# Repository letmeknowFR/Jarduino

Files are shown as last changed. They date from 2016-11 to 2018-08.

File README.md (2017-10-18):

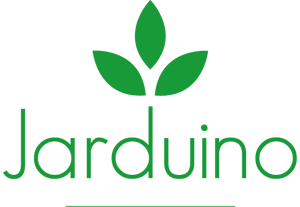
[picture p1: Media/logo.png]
Jarduino Logo


<a href="#link"> _English version below_ :us: :arrow_down: </a>

> <p align="justify">Le Jarduino est un kit DIY permettant de créer un système de culture hydroponique et automatisé pour toutes sortes de plantes. Il permet de découvrir les concepts de l'agriculture hors-sol mais également de s'initier à l'électronique, la programmation, et l'impression 3D. Ce mini jardin est à faire soi-même. Modulable, personnalisable et évolutif selon vos envies, le Jarduino est Open Source : nous fournissons à tous les fichiers nécessaires pour réaliser les pieds, les panneaux latéraux et même la carte électronique. Il est donc très simple de s'approprier le projet afin de l'améliorer ou de le personnaliser.</p>

### Bill Of Materials :bookmark_tabs:
***
| Quantité | Composant |
|:---:|:---:|
| 1 | Carte électronique |
| 1 | LCD 2 lignes 16 caractères I2C  |
| 1 | Jeu d'embases |
| 1 | Pompe USB |
| 1 | Lampe USB |
| 1 | Panier - Impression 3D |
| 1 | Pied principal - Impression 3D  |
| 1 | Panneau supérieur |
| 1 | Récipient |
| 1 | Durite |
| 1 | Alimentation |
| 3 | Pied angle - Impression 3D |
| 4 | Panneaux latéraux |

### Programmation :computer:
***
Tout d'abord placez la pile bouton (CR1220) dans son emplacement si cela n'est pas déjà fait. Ensuite, connectez l'écran à la carte principale via son connecteur, puis fixez-le à l'aide de l'embase prévue à cet effet.

Après avoir installé l'IDE Arduino, grâce au dossier fourni [software](/Software) ou directement sur le [site officiel](https://www.arduino.cc/en/Main/Software), installez les librairies qui se trouvent dans le dossier [librairies](/Software/Librairies) nécessaires à la compilation du programme principal "Jarduino.ino". Pour cela décompressez le contenu de l'archive dans votre répertoire Arduino/libraries.

Double-cliquez sur le programme ["Jarduino.ino"](/Software/Jarduino/Jarduino.ino).

Branchez votre carte via le connecteur USB, choisissez la carte "Leonardo" dans outils/type de carte et téléversez le programme !

Vous disposez également d'un programme de test ["Jarduino_test.ino"](/Software/Jarduino_Test/Jarduino_Test.ino). Il vous permettra de savoir si tous les composants électroniques fonctionnent correctement.

Vous voilà fin prêt ! Passons à la mécanique.

### Montage :wrench:
***
<p align="justify">Vous trouverez dans votre package mécanique: 3 pieds, 1 pied pour y placer la carte électronique, 4 panneaux de plastiques pour les côtés, 1 panneau pour le dessus. Montez le tout, remplissez 1/4 du récipient d'eau, ajoutez-y la lampe, la pompe, branchez l'alimentation et vous êtes fin prêt à faire pousser vos plantes.</p>

<p align="center"> Montage </p>

Vous pouvez bien sûr imprimer vos propres pieds et paniers grâce au dossier ["3D"](/3D).

### De la patience maintenant, la plante pousse ! :seedling:
***
***
<p align="center"> Jarduino Logo :us: </p>

>  <p align="justify">Jarduino is a DIY kit allowing to create a hydroponic and automated cultivation system for all kinds of plants . It allows to discover off-ground agriculture concepts and learn about electronics, programming, and 3D printing. This mini garden is a do it yourself project. Modular, customizable and scalable as you want, Jarduino is Open Source: we provide all necessary files to realize the feet, the side panels and even the electronic card. It's very simple to assimilate the project in order to improve it or to personalize it.</p>

### Bill Of Materials :bookmark_tabs:
***

| Quantity | Components |
|:---:|:---:|
| 1 | Electronic card |
| 1 | 2 line 16 character I2C LCD |
| 1 | Header |
| 1 | USB Pump |
| 1 | USB Lamp |
| 1 | Basket - 3D printed |
| 1 | Main foot - 3D printed |
| 1 | Up pannel |
| 1 | Container |
| 1 | Hose |
| 1 | Alimentation |
| 3 | Angle foot - 3D printed |
| 4 | Side pannel |

### Programming :computer:
***
First, place the button cell (CR1220) in its position if not already done. Then, connect the screen with the electronic card thanks to the 4-pin connector and fix it with the given headers.

After you installed Arduino, thanks to given folder ["software"](/Software) or the [official website](https://www.arduino.cc/en/Main/Software), install the libraries placed in the ["libraries"](/Software/Librairies) folder that make "Jarduino.ino" program compiled. To do that, uncompress the archive content in your Arduino/libraries folder.

Double-click on the program ["Jarduino.ino"](/Software/Jarduino/Jarduino.ino).

Connect the electronic card with your computer thank to the USB connector, choose "Leonardo" in tools/board option and upload the program!

You have a test program ["Jarduino_test.ino"](/Software/Jarduino_Test/Jarduino_Test.ino). It'll allow you to know if everything is ok.

You're all right! Let's move to the mechanical assembly.

### Mechanical assembly :wrench:
***
<p align="justify">You'll find in mechanical package: 3 feet, 1 main foot for the electronic card, 4 side panels, 1 panel for the top. Assemble it, fill a quarter of container with water, add the lamp, pump, power up and you're good to go!</p>

<p align="center"> Montage </p>

You can print your own 3D parts thanks to the given folder ["3D"](/3D).

### Patience now, plant is growing ! :seedling:

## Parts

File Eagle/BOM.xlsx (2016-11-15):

Name | Part | Value | Package | Description | Part NO. | Band
BAT1 | Battery holder | CR1220 | METAL-CR1220-D13.5XH5.0MM | Battery CR1220 holder
BP1 | Button | TAC_SWITCHPTH | TACTILE-PTH | Push button
C1, C2, C3 | Capacitor | 100nf 50V 10% | C0603 | Capacitor
C4, C5 | Capacitor | 100µf 50V 10% | C0603 | Capacitor
C6, C7 | Capacitor | 22pf 50V 10% | C0603 | Capacitor
D1, D2 | Diode | 1N4007 | DO-214AC | Diode
D3 | Diode | 1N4148 | LL-34 | Diode
J1 | Connector | M06POLAR | MOLEX-1X6 | Connector 6 points | Not implemented | Not implemented
J2 | Connector | M02POLAR | MOLEX-1X2 | Connector 2 points | Not implemented | Not implemented
J3, J4 | Connector | M04POLAR | MOLEX-1X4 | Connector 4 points | Not implemented | Not implemented
J5 | Connector | Double USB connector | 61400826021 | Double USB connector
J6 | Connector | AVR_SPI_PRG_6NS | 2X3-NS | Connector 2x3 points
J7 | Connector | USBPTH-VERTICAL | USB-B-PTH-VERTICAL | Connector USB type B vertical
J8 | Connector | MICRO-USB-SMD-B-(10118193-0001LF) | MICRO-USB5SMD-0.65-B Seee | Micro USB connector
K1, K2 | Relay | RELAY-HLS8L-DC5V-S-C-315030000 | 5P-L19.0XW15.0XH15.0MM | Relay 5V
L1 | Inductor | MH2028-300Y | SM-1206 | Inductor | Not implemented | Not implemented
LED1 | Rx | LEDCHIP-LED0805 | CHIP-LED0805 | led | Red LED | Generic
LED2 | Tx | LEDCHIP-LED0805 | CHIP-LED0805 | led | Red LED | Generic
LED3 | ON | LEDCHIP-LED0805 | CHIP-LED0805 | led | Green LED | Generic
Q1 | crystal | 16MHZ | HC49U | crystal
Q2 | crystal | 32.768kHz | 2P-L3.2XW1.5MM | crystal
R1, R3, R6, R7, R8 | Resistor | 1k | R0805 | Resistor | 1k | Generic
R2, R4, R5, R9, R10 | Resistor | 10k | R0805 | Resistor | 10k | Generic
R11, R12 | Resistor | 22R | R0805 | Resistor | 22R | Generic
R13, R14 | Resistor | 4k7 | R0805 | Resistor | 4k7 | Generic
T1, T2 | Transistor | S8050 | SOT23 | Transistor
U1 | Micro-controler | MCU-ATMEGA32U4(TQFP44)-AU | TQFP44-0.8-9.6X9.6MM | Micro-controler | ATMEGA32U4 | ATMEGA
U2 | RTC | DS1307ZN-1900100P1 | SOIC8 | RTC IC | DS1307ZN

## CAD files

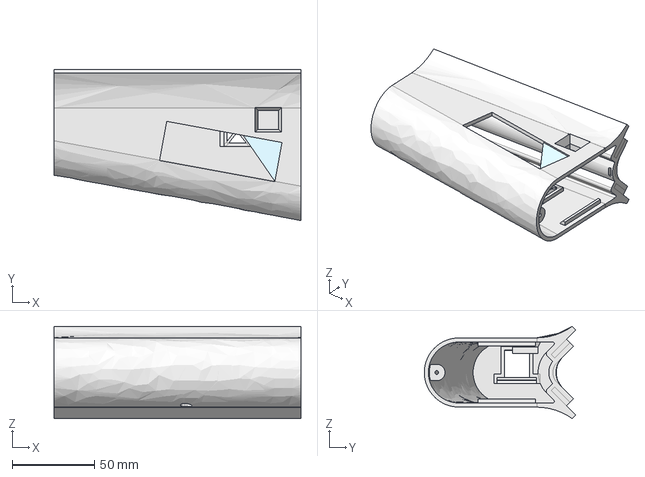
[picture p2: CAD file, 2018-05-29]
3D/pied-pcb.step
150.0 x 92.0 x 56.0 mm

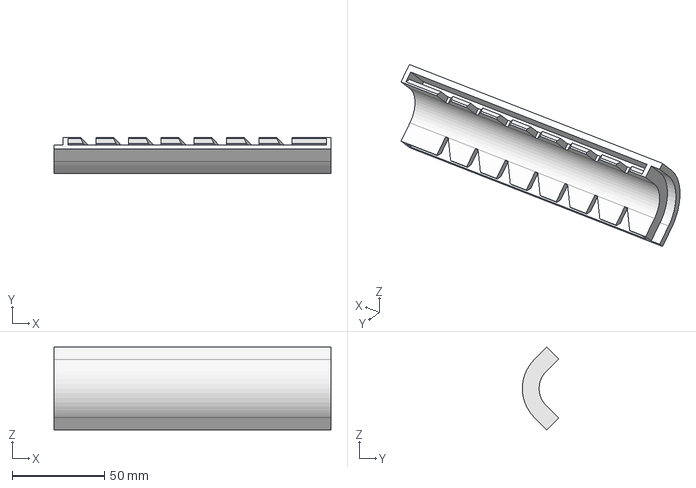
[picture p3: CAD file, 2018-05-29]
3D/pied.step
150.0 x 19.7 x 44.8 mm

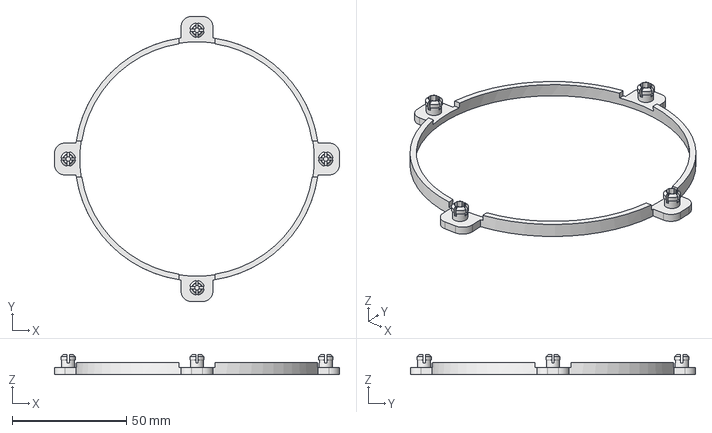
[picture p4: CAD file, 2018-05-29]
3D/bague-sup.step
125.0 x 125.0 x 8.80 mm

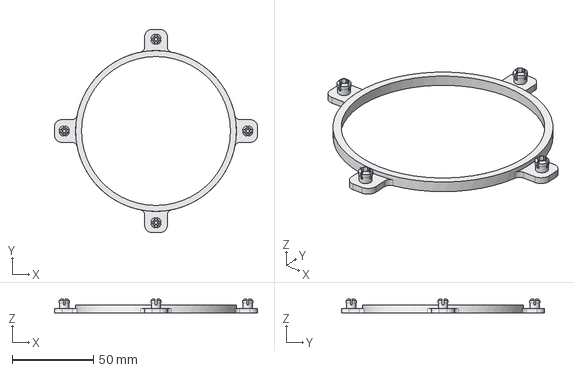
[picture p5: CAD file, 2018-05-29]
3D/bague-inf.step
125.0 x 125.0 x 8.80 mm

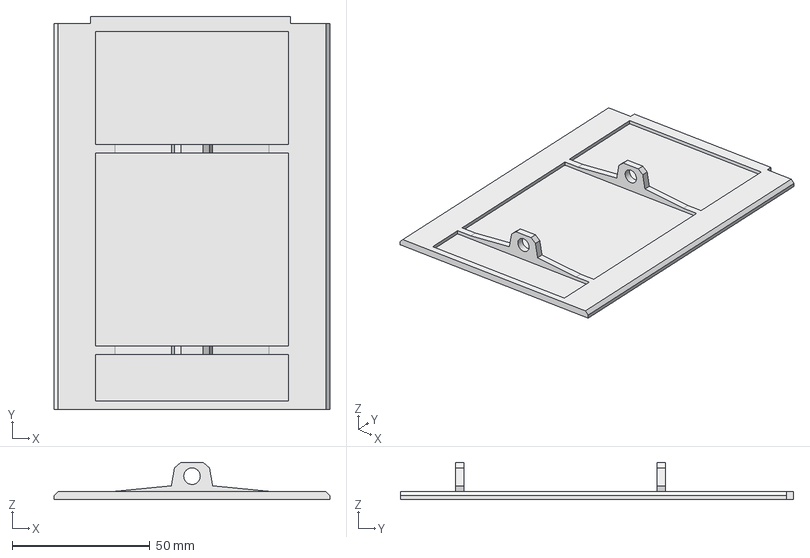
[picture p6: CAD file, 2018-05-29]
3D/cote-fixation.step
100.0 x 142.5 x 13.5 mm

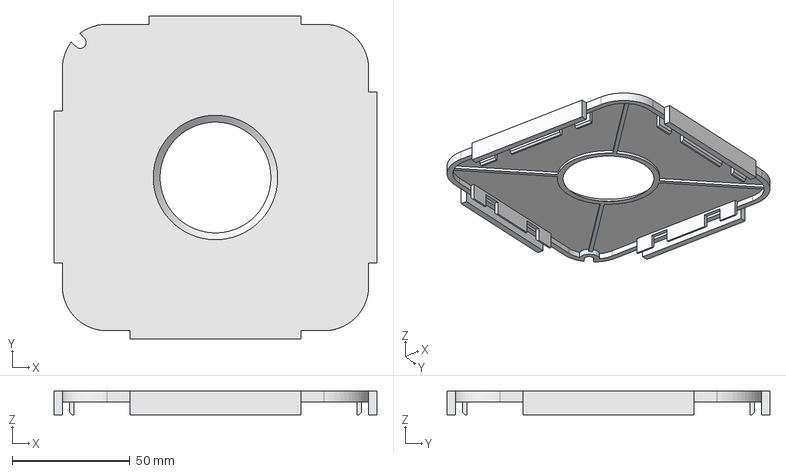
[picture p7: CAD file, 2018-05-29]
3D/face-sup.step
137.0 x 137.0 x 10.0 mm

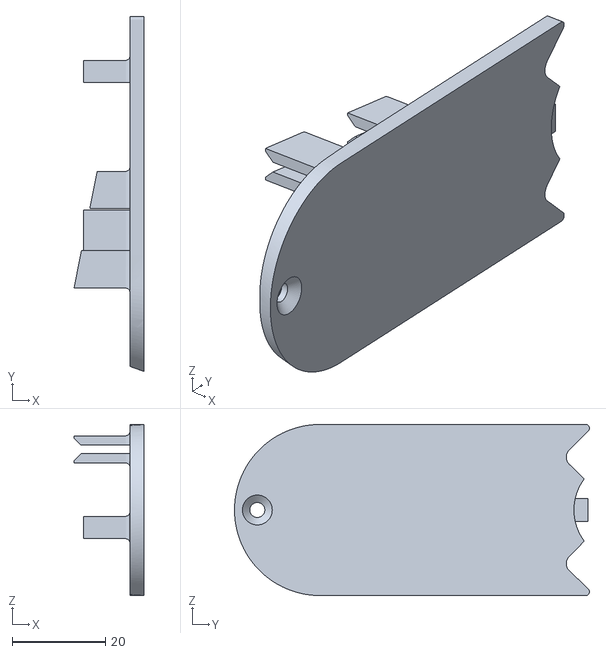
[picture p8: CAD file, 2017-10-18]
3D/couvercle-pied-ecran.stl
15.0 x 76.1 x 36.7

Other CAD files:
3D/bague-inf.stl
3D/bague-sup.stl
3D/cote-fixation.stl
3D/face-sup.stl
3D/pied-pcb.stl
3D/pied.stl

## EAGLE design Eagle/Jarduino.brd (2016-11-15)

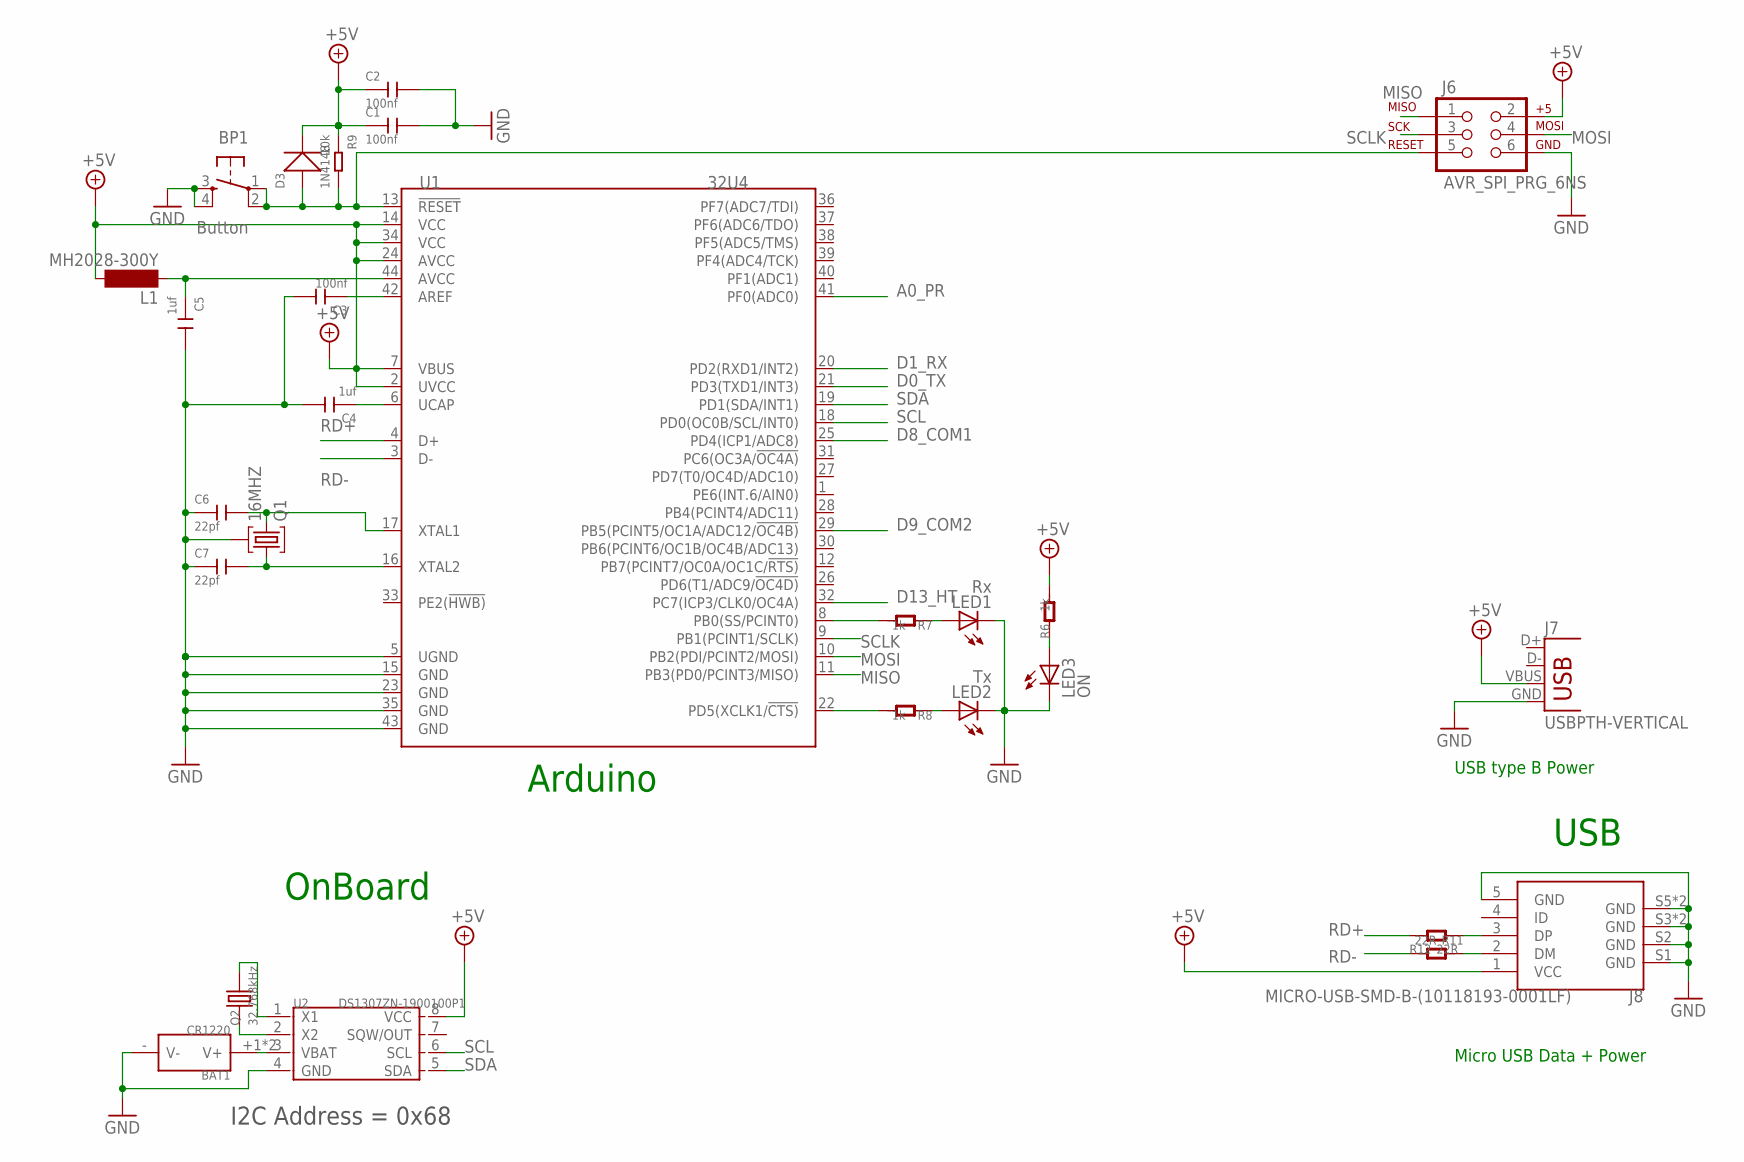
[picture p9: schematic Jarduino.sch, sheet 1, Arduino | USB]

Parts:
BAT1: CR1220; METAL-CR1220-D13.5XH5.0MM
BP1: Button; TACTILE-PTH
C1, C2, C3: 100nf; C0603
C4, C5: 1uf; C0603
C6, C7: 22pf; C0603
D3: 1N4148; LL-34
J6: AVR_SPI_PRG_6NS; 2X3-NS
J7: USBPTH-VERTICAL; USB-B-PTH-VERTICAL
J8: MICRO-USB-SMD-B-(10118193-0001LF); MICRO-USB5+6P-SMD-0.65-B
L1: MH2028-300Y; SM-1206
LED1: Rx; CHIP-LED0805
LED2: Tx; CHIP-LED0805
LED3: ON; CHIP-LED0805
Q1: 16MHZ; HC49U
Q2: 32.768kHz; 2P-L3.2XW1.5MM
R6, R7, R8: 1k; R0805
R9: 10k; R0805
R11, R12: 22R; R0805
U1: 32U4; TQFP44-0.8-9.6X9.6MM
U2: DS1307ZN-1900100P1; SOIC8

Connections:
+5V: C1.1, C2.1, D3.C (-), J6.2, J7.VBUS, J8.1 (VCC), L1.2, R6.2, R9.1, U1.2 (UVCC), U1.7 (VBUS), U1.14 (VCC), U1.24 (AVCC), U1.34 (VCC), U2.8 (VCC); also elsewhere on the board
A0_PR: U1.41 (PF0(ADC0)); also elsewhere on the board
D0_TX: U1.21 (PD3(TXD1/INT3)); also elsewhere on the board
D1_RX: U1.20 (PD2(RXD1/INT2)); also elsewhere on the board
D8_COM1: U1.25 (PD4(ICP1/ADC8)); also elsewhere on the board
D9_COM2: U1.29 (PB5(PCINT5/OC1A/ADC12/!OC4B)); also elsewhere on the board
D13_HT: U1.32 (PC7(ICP3/CLK0/OC4A)); also elsewhere on the board
GND: BAT1.- (V-), BP1.3, BP1.4, C1.2, C2.2, C3.2, C4.2, C5.2, C6.1, C7.1, J6.6, J7.GND, J8.5 (GND), J8.S1 (GND), J8.S2 (GND), J8.S3 (GND), J8.S4 (GND), J8.S5 (GND), J8.S6 (GND), LED1.C, LED2.C, LED3.C, Q1.2, U1.5 (UGND), U1.15 (GND), U1.23 (GND), U1.35 (GND), U1.43 (GND), U2.4 (GND); also elsewhere on the board
MISO: J6.1, U1.11 (PB3(PD0/PCINT3/MISO))
MOSI: J6.4, U1.10 (PB2(PDI/PCINT2/MOSI))
unnamed: LED3.A, R6.1
unnamed: R7.2, U1.8 (PB0(SS/PCINT0))
unnamed: J8.2 (DM), R12.2
unnamed: R8.2, U1.22 (PD5(XCLK1/!CTS))
unnamed: LED1.A, R7.1
unnamed: LED2.A, R8.1
unnamed: C6.2, Q1.3, U1.17 (XTAL1)
unnamed: C4.1, U1.6 (UCAP)
unnamed: C5.1, L1.1, U1.44 (AVCC)
unnamed: C3.1, U1.42 (AREF)
unnamed: C7.2, Q1.1, U1.16 (XTAL2)
unnamed: J8.3 (DP), R11.1
unnamed: Q2.2, U2.1 (X1)
unnamed: Q2.1, U2.2 (X2)
unnamed: BAT1.+1 (V+), BAT1.+2 (V+), U2.3 (VBAT)
RD+: R11.2, U1.4 (D+)
RD-: R12.1, U1.3 (D-)
RESET: BP1.1, BP1.2, D3.A (+), J6.5, R9.2, U1.13 (!RESET)
SCL: U1.18 (PD0(OC0B/SCL/INT0)), U2.6 (SCL); also elsewhere on the board
SCLK: J6.3, U1.9 (PB1(PCINT1/SCLK))
SDA: U1.19 (PD1(SDA/INT1)), U2.5 (SDA); also elsewhere on the board

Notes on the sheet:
Arduino
I2C Address = 0x68
OnBoard
USB
Micro USB Data + Power
USB type B Power

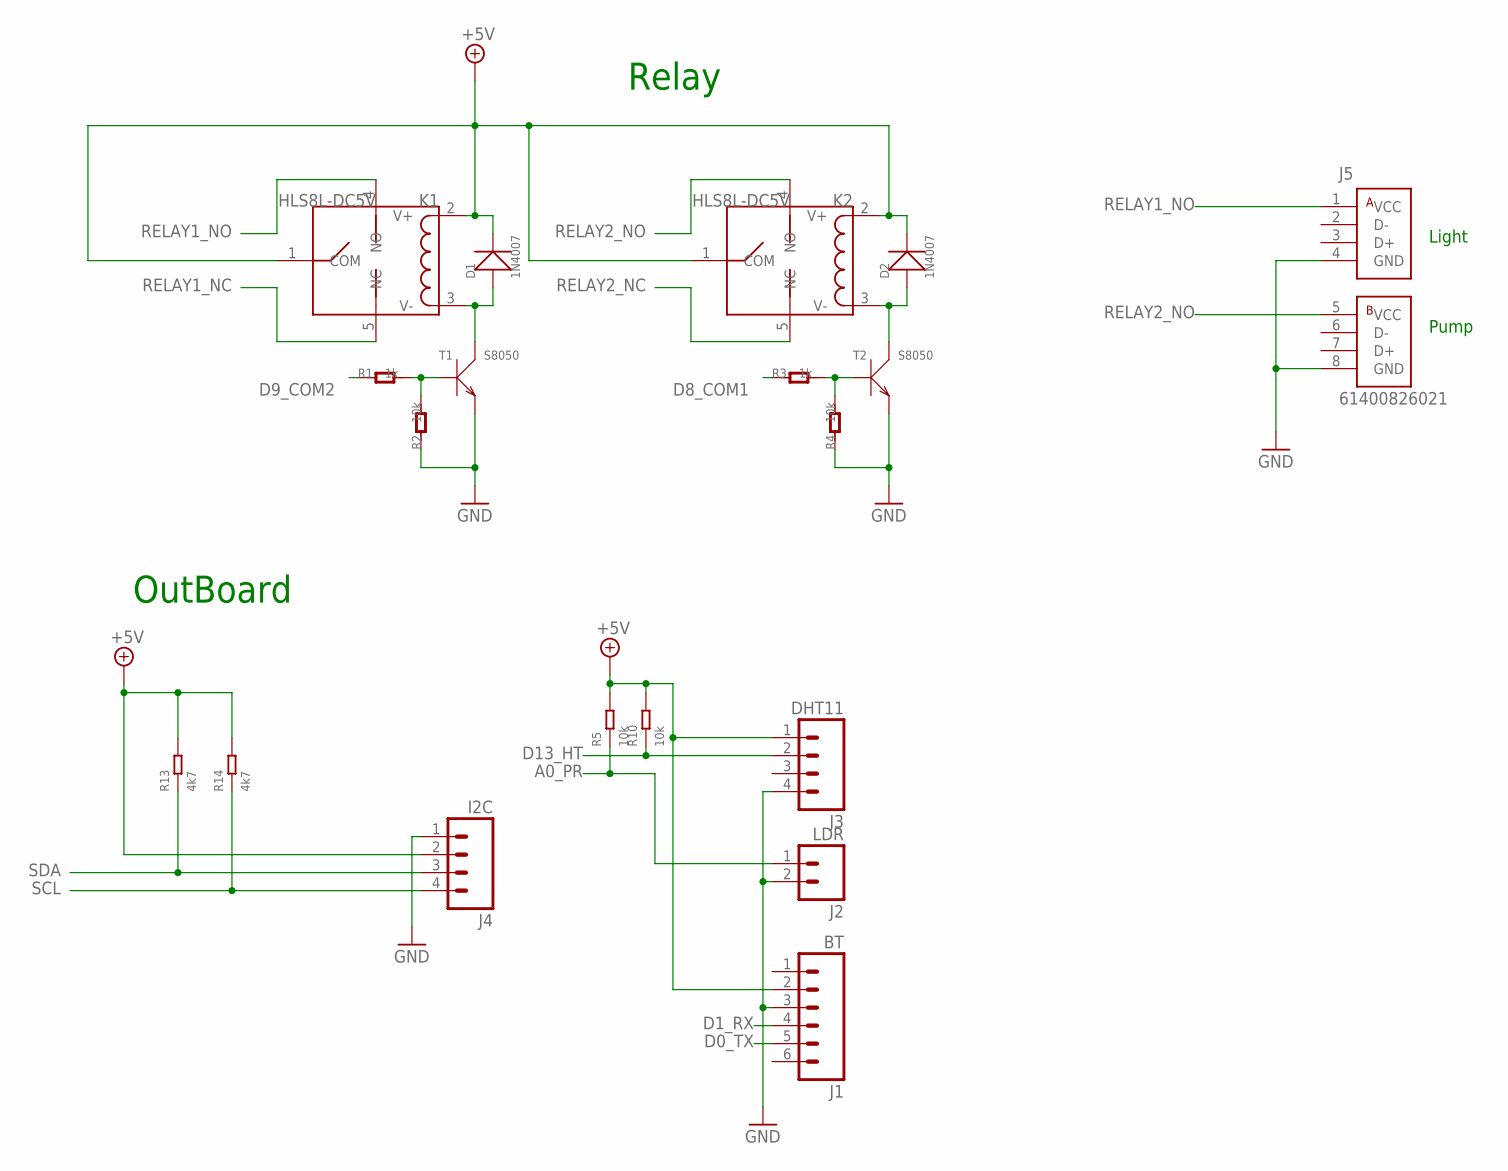
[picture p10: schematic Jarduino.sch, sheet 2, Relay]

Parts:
D1, D2: 1N4007; DO-214AC
J1: BT; MOLEX-1X6
J2: LDR; MOLEX-1X2
J3: DHT11; MOLEX-1X4
J4: I2C; MOLEX-1X4
J5: 61400826021
K1, K2: HLS8L-DC5V; 5P-L19.0XW15.0XH15.0MM
R1, R3: 1k; R0805
R2, R4, R5, R10: 10k; R0805
R13, R14: 4k7; R0805
T1, T2: S8050; SOT23

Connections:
+5V: D1.2 (-), D2.2 (-), J1.2, J3.1, J4.2, K1.1 (COM), K1.2 (V+), K2.1 (COM), K2.2 (V+), R5.2, R10.2, R13.2, R14.2; also elsewhere on the board
A0_PR: J2.1, R5.1; also elsewhere on the board
D0_TX: J1.5; also elsewhere on the board
D1_RX: J1.4; also elsewhere on the board
D8_COM1: R3.1; also elsewhere on the board
D9_COM2: R1.1; also elsewhere on the board
D13_HT: J3.2, R10.1; also elsewhere on the board
GND: J1.3, J2.2, J3.4, J4.1, J5.4 (GND), J5.8 (GND), R2.1, R4.1, T1.2 (E), T2.2 (E); also elsewhere on the board
unnamed: R3.2, R4.2, T2.1 (B)
unnamed: D2.1 (+), K2.3 (V-), T2.3 (C)
unnamed: R1.2, R2.2, T1.1 (B)
unnamed: D1.1 (+), K1.3 (V-), T1.3 (C)
RELAY1_NC: K1.5 (NC)
RELAY1_NO: J5.1 (VCC), K1.4 (NO)
RELAY2_NC: K2.5 (NC)
RELAY2_NO: J5.5 (VCC), K2.4 (NO)
SCL: J4.4, R14.1; also elsewhere on the board
SDA: J4.3, R13.1; also elsewhere on the board

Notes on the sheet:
Relay
OutBoard
Light
Pump

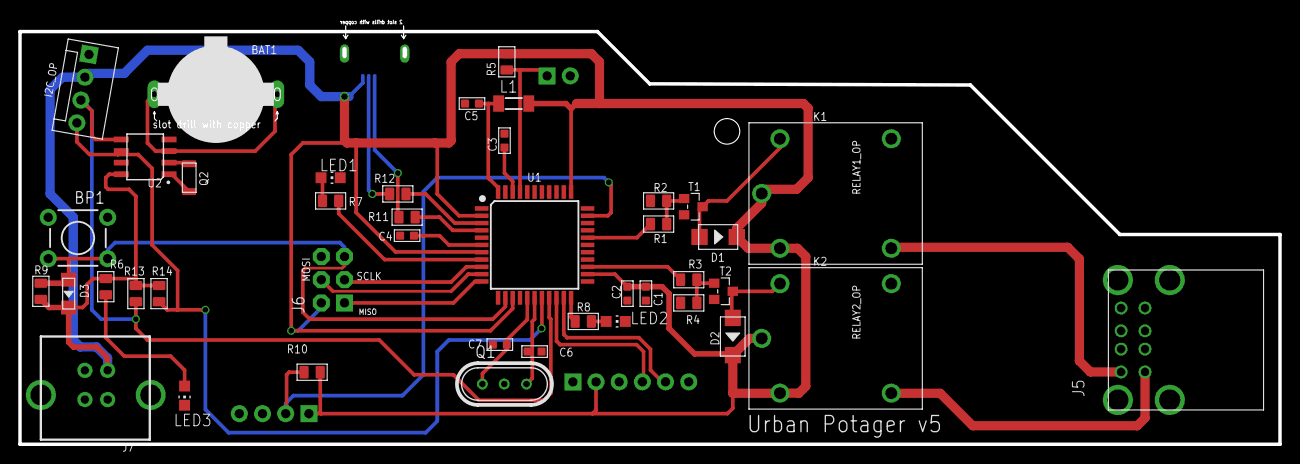
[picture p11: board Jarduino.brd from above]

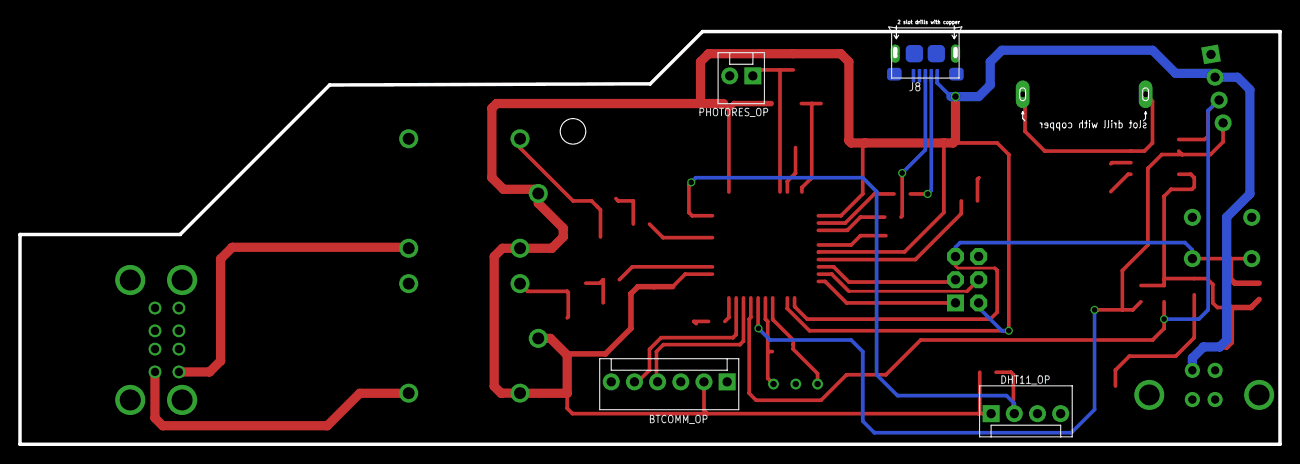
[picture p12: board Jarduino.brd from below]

Board: 2 copper layers, 138.1 x 45.8 mm, 46 parts (4 on the bottom side), 37 nets.

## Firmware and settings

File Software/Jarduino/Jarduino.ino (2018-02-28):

/*******************************************************************/
/********************* The Jarduino ********************************/
/*******************************************************************/

#include <Wire.h>
#include <Time.h>
#include <dht11.h>
#include <avr/wdt.h>
#include <DS1307RTC.h>
#include <LiquidCrystal_I2C.h>

/********************* CONFIGURATION ******************************/

//#define DEBUG   1      // Debug Mode
#define LUXMIN 70        // Luminosité maximale
#define LUXMAX 50        // Luminosité minimale
#define HourMax 22       // Heure d'éteinte du Jarduino
#define HourMin 8        // Heure de démmarage du Jarduino
#define Startingdelay 500// Temps entre icone au démarrage

/********************* FIN CONFIGURATION **************************/

#define PIN_LUX A5        // LUX pin
#define BACKLIGHT_PIN 3   // LCD Screen Light
#define I2C_ADDR 0x27     // LCD Screen Adress
#define PIN_RELAY1 4      // Relais de commande pompe
#define PIN_RELAY2 9      // Relais de commande lumière
#define DHT11PIN 13       // Pin du capteur d'humidité / temperature
#define MOY 3             // Nombre de valeurs utilisées pour les moyennes de mesures

#ifdef DEBUG
#define PIN_TX 0          // Inutile de la définir comme entrée sortie sera fait par le Serial.begin
#define PIN_RX 1          // Inutile de la définir comme entrée sortie sera fait par le Serial.begin
#endif

LiquidCrystal_I2C  lcd(I2C_ADDR, 16, 2);// LCD creation
dht11 DHT11;                            // Creation de l'entité DHT11
tmElements_t tm,tm2;                    // Horloge + Horloge comparaison
int TempAndHum;                         // Température + humidité
boolean pumpon=false,lighton=false,pumplcd=false,pumplcdalreadyon=false,AfterWateringOrInit=false;
byte WateringTimeLCD,LuxPercent,LuxPercentOld,MinuteOld,Humidity,HumidityOld,Temperature,TemperatureOld=1;
const char *monthName[12] = {"Jan","Feb","Mar","Apr","May","Jun","Jul","Aug","Sep","Oct","Nov","Dec"};
/********************************* LOGO **************************/

byte water[8] = 
{
  B00100,
  B01110,
  B01110,
  B11111,
  B11101,
  B11111,
  B01110,
  B00000,
};  
byte humidity[8] = 
{
  B01110,
  B11111,
  B01110,
  B10000,
  B00101,
  B10000,
  B00001,
  B00000,
};
byte light[8] = 
{
  B00010,
  B00100,
  B01100,
  B11111,
  B00110,
  B00100,
  B01000,
  B00000,
};  
byte temp[8] = 
{
  B00100,
  B01010,
  B01010,
  B01110,
  B11111,
  B11111,
  B01110,
};
/***************************** FIN LOGO **************************/

/***************************** INIT ******************************/
void setup() {
  wdt_enable(WDTO_8S); // Watchdog de 8s
  
  #ifdef DEBUG
  bool parse=false;
  bool config=false;
  #endif

  // get the date and time the compiler was run
  if (getDate(__DATE__) && getTime(__TIME__)) {
    #ifdef DEBUG
    parse = true;
    #endif
    
    RTC.read(tm2); //Lecture du RTC Chip 2
    #ifdef DEBUG
    Serial.print("Lecture + tm2");
    delay(10000);
    #endif
    
    if((tm.Year > tm2.Year) || (tm.Year == tm2.Year && tm.Month > tm2.Month) ||
       (tm.Year == tm2.Year && tm.Month == tm2.Month && tm.Day > tm2.Day) ||
       (tm.Year == tm2.Year && tm.Month == tm2.Month && tm.Day == tm2.Day && tm.Hour > tm2.Hour) ||
       (tm.Year == tm2.Year && tm.Month == tm2.Month && tm.Day == tm2.Day && tm.Hour == tm2.Hour && tm.Minute > tm2.Minute)) {
      if (RTC.write(tm)) {
        #ifdef DEBUG
        config = true;
        Serial.println("Update"); 
        #endif
      }
    }
  }
  
  #ifdef DEBUG
  Serial.begin(9600);
  while (!Serial) ;
  delay(100);
  Serial.print("The Jarduino demarre... \n\n");
  if (parse && config) {
    Serial.print("RTC chip configure avec: Heure=");
    Serial.print(__TIME__);
    Serial.print(", Date=");
    Serial.println(__DATE__);
  } else if (parse)
      Serial.println("Pas de mise a jour de la RTC\n");
    else
      Serial.print("Erreur de communication avec le RTC chip\n");
  #endif
  
  Wire.begin();
  lcd_initialisation();
  lcd.createChar(0, water);
  lcd.createChar(1, light);
  lcd.createChar(2, humidity);
  lcd.createChar(3, temp);
  lcd.backlight();
  lcd.setCursor(4, 0);
  lcd.print("JARDUINO");
  delay(Startingdelay);
  lcd.setCursor(0, 1);
  lcd.print("   ");
  lcd.write(byte(3));
  delay(Startingdelay);
  lcd.print("  ");
  lcd.write(byte(2));
  delay(Startingdelay);
  lcd.print("  ");
  lcd.write(byte(1));
  delay(Startingdelay);
  lcd.print("  ");
  lcd.write(byte(0));
  delay(Startingdelay);
  lcd.clear();
  AfterWateringOrInit = true;
  
  pinMode(PIN_RELAY1,OUTPUT);
  digitalWrite(PIN_RELAY1,LOW);
  pinMode(PIN_RELAY2,OUTPUT);
  digitalWrite(PIN_RELAY2,LOW);
}
/************************* FIN INIT ******************************/

/***************************** LOOP ******************************/
void loop() {
  wdt_reset(); // Reset Watchdog
  
  RTC.read(tm); //Lecture du RTC Chip
  GetSensorsValues();
  WateringTimeCalcul();
  Light();
  Pump();
  LCDDisplay();
  
  #ifdef DEBUG
  Serial.print("Pompe: ");
  Serial.print(pumpon);
  Serial.print(" | ");
  Serial.print("Lumiere: ");
  Serial.print(lighton);
  Serial.print(" | ");
  Serial.print("Pompe LCD: ");
  Serial.print(pumplcd);
  Serial.print(" | ");
  Serial.print("Temps arrosage: ");
  Serial.print(WateringTimeLCD);
  Serial.print(" | ");
  print2digitsSERIAL(tm.Hour);
  Serial.write(':');
  print2digitsSERIAL(tm.Minute);
  Serial.write(':');
  print2digitsSERIAL(tm.Second);
  Serial.print("\n");
  #endif
  
  LuxPercentOld = LuxPercent;
  HumidityOld = Humidity;
  TemperatureOld = Temperature;
  MinuteOld = tm.Minute;
  delay(500);
}
/************************* FIN LOOP ******************************/

/***************** RECUPERATION HEURE/DATE ***********************/
bool getTime(const char *str){
  int Hour, Min, Sec;

  if (sscanf(str, "%d:%d:%d", &Hour, &Min, &Sec) != 3) return false;
  tm.Hour = Hour;
  tm.Minute = Min;
  tm.Second = Sec;
  return true;
}

bool getDate(const char *str){
  char Month[12];
  int Day, Year;
  uint8_t monthIndex;

  if (sscanf(str, "%s %d %d", &Month, &Day, &Year) != 3) return false;
  for (monthIndex = 0; monthIndex < 12; monthIndex++) {
    if (strcmp(Month, monthName[monthIndex]) == 0) break;
  }
  if (monthIndex >= 12) return false;
  tm.Day = Day;
  tm.Month = monthIndex + 1;
  tm.Year = CalendarYrToTm(Year);
  return true;
}
/*************** END RECUPERATION HEURE/DATE ***********************/

/************************* 2 DIGITS ******************************/
//Permet d'aficher un 0 avant un chiffre en dessous de 10
#ifdef DEBUG
void print2digitsSERIAL(int number) {
  if (number >= 0 && number < 10) {
    Serial.write('0');
  }
  Serial.print(number);
}
#endif

void print2digitsLCD(byte number) {
  if (number >= 0 && number < 10) {
     lcd.print("0");
  }
   lcd.print(number);
}
/*********************** FIN 2 DIGITS ****************************/

/************************* VALEURS CAPTEURS **********************/
void GetSensorsValues() {
  int Reading = analogRead(PIN_LUX);                              // Récupérer la valeur du capteur de luminosité
  Reading = map(Reading, 0, 1000, 100, 0);                        // Ramener la valeur entre 0 et 100
  LuxPercent = (Reading + LuxPercent * MOY)/(MOY + 1);            // Moyenner la valeur
  TempAndHum = DHT11.read(DHT11PIN);                              // Récupérer la valeur du capteur de température / humidité
  Humidity = (DHT11.humidity + Humidity * MOY)/(MOY + 1);         // Moyenner la valeur de l'humidité
  Temperature = (DHT11.temperature + Temperature * MOY)/(MOY + 1);// Moyenner la valeur de temperature
  
  #ifdef DEBUG
  Serial.print("Luminosite: ");
  Serial.print(LuxPercent);
  Serial.print(" | ");
  Serial.print("Humidite: ");
  Serial.print(Humidity);
  Serial.print(" | ");
  Serial.print("Temperature: ");
  Serial.print(Temperature);
  Serial.print(" | ");
  #endif
}
/******************** FIN VALEURS CAPTEURS ***********************/

/************************* POMPE *********************************/
void Pump() {
  if (tm.Minute == 0 || tm.Minute == 20 || tm.Minute == 40){
    if (tm.Second > 0 && tm.Second <= 20){
      if (pumpon == false){
        digitalWrite(PIN_RELAY1, HIGH);
        pumpon = true;
        pumplcd = true;
      }
    } else {
      if (pumpon == true){
        digitalWrite(PIN_RELAY1, LOW);
        pumpon = false;
        pumplcd = false;
        pumplcdalreadyon = false;
        lcd.clear();
        AfterWateringOrInit = true;
      }
    }
  } else {
    if (pumpon == true || digitalRead(PIN_RELAY1) == HIGH){
      digitalWrite(PIN_RELAY1, LOW);
      pumpon = false; 
      pumplcd = false;
      pumplcdalreadyon = false;
    }
  }
}
/************************** FIN POMPE ****************************/

/**************************** LUMIERE ****************************/
void Light() {
  if (tm.Hour <= HourMax && tm.Hour >= HourMin){
      if (LuxPercent >= LUXMIN){
        if (lighton == true){
            digitalWrite(PIN_RELAY2, LOW);
            lighton = false;
            pumplcd=false;
        }
      } else {
        if (LuxPercent <= LUXMAX){
          if (lighton == false){
            digitalWrite(PIN_RELAY2, HIGH);
            lighton = true;
          }
        }
      }
  } else {
    if (lighton == true || digitalRead(PIN_RELAY2) == HIGH) {
      digitalWrite(PIN_RELAY2, LOW);
      lighton = false;
    }
  }
}
/************************* FIN LUMIERE ***************************/

/************************* AFFICHAGE LCD *************************/
void LCDDisplay() {
  if (pumpon == true && pumplcd == true && pumplcdalreadyon == false) {
    lcd.clear();
    lcd.setCursor(1, 0);
    lcd.write(byte(2));
    lcd.print("  WATERING  ");
    lcd.write(byte(2));
    lcd.setCursor(0, 1);
    lcd.write(byte(2));
    lcd.print(" IN PROGRESS  ");
    lcd.write(byte(2)); 
    pumplcdalreadyon = true;
  } else if (pumpon == true && pumplcd == true) {
    lcd.setCursor(1, 0);
    lcd.write(byte(2));
    lcd.print("  WATERING  ");
    lcd.write(byte(2));
    
    lcd.setCursor(0, 1);
    lcd.write(byte(2));
    lcd.print(" IN PROGRESS  ");
    lcd.write(byte(2)); 
  } else {
    if(AfterWateringOrInit == true){
        lcd.clear();
        lcd.setCursor(0,0);
        print2digitsLCD(tm.Hour);
        lcd.print(':');
        print2digitsLCD(tm.Minute);
        lcd.setCursor(11,0);
        lcd.write(byte(2));
        print2digitsLCD(WateringTimeLCD);
        lcd.print("mn");
        lcd.setCursor(6,1);
        lcd.write(byte(0));
        print2digitsLCD(Humidity);
        lcd.print("%");
        lcd.setCursor(0,1);
        lcd.write(byte(3));
        print2digitsLCD(Temperature);
        lcd.print((char)223);
        lcd.print("C");
        lcd.setCursor(12,1);
        lcd.write(byte(1));
        print2digitsLCD(LuxPercent);
        lcd.print("%");
        AfterWateringOrInit = false;
    } else{
      if(tm.Minute != MinuteOld){
        lcd.setCursor(0,0);
        print2digitsLCD(tm.Hour);
        lcd.print(':');
        print2digitsLCD(tm.Minute);
        lcd.setCursor(11,0);
        lcd.write(byte(2));
        print2digitsLCD(WateringTimeLCD);
        lcd.print("mn");
      }
      if(Humidity != HumidityOld){
        lcd.setCursor(6,1);
        lcd.write(byte(0));
        print2digitsLCD(Humidity);
        lcd.print("%");
      }
      if(Temperature != TemperatureOld){
        lcd.setCursor(0,1);
        lcd.write(byte(3));
        print2digitsLCD(Temperature);
        lcd.print((char)223);
        lcd.print("C");
      }
      if(LuxPercent != LuxPercentOld){
        lcd.setCursor(12,1);
        lcd.write(byte(1));
        print2digitsLCD(LuxPercent);
        lcd.print("%");
      }
    }
   }
}
/********************** FIN AFFICHAGE LCD ************************/

/******************* CALCUL TEMPS ARROSAGE ***********************/
void WateringTimeCalcul()
{ 
  WateringTimeLCD = 20 - (tm.Minute % 20); // Nombre de minutes avant le prochain arrosage
}
/****************** FIN CALCUL TEMPS ARROSAGE ********************/

/****************** LCD INIT *************************************/
void lcd_initialisation() { // Fonction d'initlisation LCD
  byte error, address;
  byte I2CIC1 = 0x68;

  #ifdef DEBUG
  Serial.println("Scanning...");
  #endif
 
  for(address = 1; address < 127; address++ )
  {
    // The i2c_scanner uses the return value of
    // the Write.endTransmisstion to see if
    // a device did acknowledge to the address.
    Wire.beginTransmission(address);
    error = Wire.endTransmission();
 
    if (error == 0)
    {
      if(address != I2CIC1) {
        lcd.change_address(address);
      }
    }
  }
  lcd.init();
}
/****************** FIN LCD INIT *********************************/

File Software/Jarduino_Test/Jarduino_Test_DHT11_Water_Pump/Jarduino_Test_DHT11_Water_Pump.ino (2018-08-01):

/*******************************************************************/
/*********** The Jarduino Test DHT11 + Water Pump ******************/
/*******************************************************************/

#include <dht11.h>                            // Ajout de la librairie nécessaire pour l'utilisation de capteur DHT11
#include <LiquidCrystal_I2C.h>                // Ajout de la librairie nécessaire pour l'utilisation de l'écran LCD
#include <Wire.h>                             // Ajout de la librairie nécessaire pour la communication I2C
#include <Time.h>
#include <DS1307RTC.h>

#define PRINT 1                               // Affichage : LCD(1) - Moniteur série(0) 
#define MOY 3                                 // Nombre de valeurs utilisées pour les moyennes de mesures
#define DHT11PIN 13                           // Pin du capteur d'humidité / temperature
#define BACKLIGHT_PIN 3                       // Pin d'alimentation de l'écran LCD
#define I2C_ADDR 0x27                         // Adresse de l'I2C
#define PIN_RELAY1 4                          // Pin du relais de la pompe

LiquidCrystal_I2C  lcd(I2C_ADDR, 16, 2);      // Création de l'écran LCD
dht11 DHT11;                                  // Création de l'entité DHT11
int   TempAndHum;                             // Déclaration d'une variable température / humidité
byte  Humidity,Temperature = 1;               // Déclaration de deux variables humidité + température
tmElements_t tm,tm2;                          // tmElements est une structure contenant plusieurs information remplie grâce à la fonction RTC.read()

/***************************** INIT ******************************/
void setup() {
  Serial.begin(9600);                         // Initialisation du moniteur série (Outils/Moniteur série)
  Wire.begin();                               // Initialisation de l'I2C
  lcd_initialisation();                       // Initialisation de l'écran LCD
  lcd.backlight();                            // Initialisation du rétro-éclairage de l'écran LCD
  RTC.read(tm2);                              // Lecture du RTC chip (Real Time Clock)
  tm2.Minute = tm2.Minute + 2;                // Arrosage toutes les 2 minutes
  pinMode(PIN_RELAY1, OUTPUT);                // Configure le pin spécifié pour qu'il se comporte en sortie
  digitalWrite(PIN_RELAY1, LOW);              // Met un niveau logique BAS sur le pin spécifié
}
/***************************** FIN INIT **************************/

/***************************** LOOP ******************************/
void loop() {
  TempAndHum = DHT11.read(DHT11PIN);                                        // Récupérer la valeur du capteur de température / humidité
  Humidity = (DHT11.humidity + Humidity * MOY)/(MOY + 1);                   // Moyenner la valeur de l'humidité
  Temperature = (DHT11.temperature + Temperature * MOY)/(MOY + 1);          // Moyenner la valeur de temperature
  RTC.read(tm);                                                             // Lecture du RTC chip (Real Time Clock), rempli la structure tmElements

  #ifdef PRINT                                                              // Si affichage sur l'écran LCD
    lcd.clear();                                                            // Nettoyage de l'écran
    lcd.setCursor(0, 0);                                                    // On place le curseur en haut à gauche de l'écran
    lcd.print("Arrosage: ");                                                // Affichage de l'heure du future arrosage
    print2digitsLCD(tm.Hour);
    lcd.print(":");
    print2digitsLCD(tm2.Minute);
    lcd.setCursor(0, 1);                                                    // On place le curseur à la ligne inférieur
    lcd.print(Humidity);                                                    // Affichage du pourcentage d'humidité
    lcd.print("%");
  #endif
  Serial.print("Arrosage à ");                                              // Affichage sur le moniteur série du future arrosage + humidité
  Serial.print(tm2.Hour);
  Serial.print(":");
  Serial.print(tm2.Minute);
  Serial.print(" - Humidité : ");
  Serial.println(Humidity);
  if (tm2.Minute == tm.Minute && tm2.Hour == tm.Hour) {                     // Si c'est l'heure d'arroser
    if (Humidity < 50) {                                                    // Si l'humidité est inférieur à 50% on arrose
      tm2.Hour = tm.Hour;
      digitalWrite(PIN_RELAY1, HIGH);                                       // Mise en marche de la pompe
      Serial.println("Pompe ON");                                           // Affichage sur le moniteur série
      #ifdef PRINT                                                          // Si affichage sur l'écran LCD
        lcd.setCursor(0, 1);                                                // On place le curseur à la ligne inférieur
        lcd.print("Pompe ON");
      #endif
      delay(2000);                                                          // Arrosage de deux secondes
      digitalWrite(PIN_RELAY1, LOW);                                        // Arrèt de la pompe
    }
    tm2.Minute = tm.Minute + 2;                                             // Arrosage toutes les 2 minutes
  }
}
/***************************** FIN LOOP **************************/

/************************* 2 DIGITS ******************************/
void print2digitsLCD(byte number) {                   //Permet d'aficher un 0 avant un chiffre en dessous de 10
  if (number >= 0 && number < 10) {
     lcd.print("0");
  }
   lcd.print(number);
}
/*********************** FIN 2 DIGITS ****************************/

/****************** LCD INIT *************************************/
void lcd_initialisation() {                           // Fonction d'initlisation de l'écran LCD
  byte error, address;
  byte I2CIC1 = 0x68;

  for (address = 1; address < 127; address++ ) {
    Wire.beginTransmission(address);                  // L'i2c_scanner utilise la valeur de retournée par la fonction Write.endTransmisstion,
    error = Wire.endTransmission();                   // Afin de déterminer si un composant est assigné à l'adresse retourné.
    if (error == 0) {                                 // Si la transmission est un succés et
      if (address != I2CIC1)                          // Si différent de l'I2C alors on change l'adresse.
        lcd.change_address(address);
    }
  }
  lcd.init();                                         // Initialisation de l'écran LCD
}
/****************** FIN LCD INIT *********************************/

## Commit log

2017-12-03 Add Freecad files
    Freecad sources of the STL files
    [jarduino.FCStd]
2018-02-28 Fixed a bug where the RTC would go back to the time/date of compilation after MCU reset. Ticket #310933
    [Jarduino.ino]
2018-05-29 Mise à jour des fichiers d'impressions
    [Couvercle_Pied_Ecran.stl, Panier.STL, Pied_Angle.STL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]

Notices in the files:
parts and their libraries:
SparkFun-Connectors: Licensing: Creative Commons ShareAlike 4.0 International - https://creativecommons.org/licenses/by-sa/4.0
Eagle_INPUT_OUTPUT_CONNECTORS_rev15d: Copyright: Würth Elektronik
